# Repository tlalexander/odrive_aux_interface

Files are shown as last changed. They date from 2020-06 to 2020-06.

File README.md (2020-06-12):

Meow I'm a cat.

This repo contains Kicad files for an Odrive auxiliary interface board.

This board plugs in to your Odrive and gives you JST-XH connectors for the GPIO.

This is version 1.2 (see previous commits for older versions).
1.2 uses an ethernet cable and RS-485 for interface for communications.
1.2 also features an e-stop circuit which must be driven by a square wave.

See parts_list.txt for a parts list for the older V1.1. See the current schematic for part info on 1.2.

Order the older V1.1 PCB directly from OSHPark here:
https://oshpark.com/shared_projects/oXQvdpD9

This board was designed by Taylor Alexander for Twisted Fields LLC.
Big thanks to Daniel Theobald for funding the work.

This work is licensed CC0 aka Public Domain. Use this information for any purpose.

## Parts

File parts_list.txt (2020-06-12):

MY APOLOGIES BUT THIS DOCUMENT IS OUT OF DATE FOR v1.2

36-5015CT-ND‎
‎5015‎
Keystone Electronics
PC TEST POINT MINIATURE 

455-2270-ND‎
‎B5B-XH-A(LF)(SN)‎
JST Sales America Inc.
CONN HEADER VERT 5POS 2.5MM

952-3302-ND‎
‎M20-9991245‎
Harwin Inc.
CONN HEADER VERT 12POS 2.54MM 

-------

455-3241-ND‎
‎ASXHSXH22K305‎
JST Sales America Inc.
JUMPER SXH-001T-P0.6 X2 12"

455-2268-ND‎
‎XHP-5‎
JST Sales America Inc.
CONN HOUSING 2.5MM 5POS

455-2266-ND
JST XH 2 Pin Housing

455-2219-ND
JST XH 3 Pin Housing

455-2267-ND
JST XH 4 Pin Housing

-------------

1080-1602-1-ND
EL814S1(A)(TA)-V
OPTOISOLTR 5KV TRANSISTOR 4-SMD 

P20KDACT-ND
20k 0805 resistor

455-2271-ND‎
‎B6B-XH-A(LF)(SN)‎
JST Sales America Inc.
CONN HEADER VERT 6POS 2.5MM

455-2249-ND‎
‎B4B-XH-A(LF)(SN)‎
JST Sales America Inc.
CONN HEADER VERT 4POS 2.5MM

455-2248-ND‎
‎B3B-XH-A(LF)(SN)‎
JST Sales America Inc.
CONN HEADER VERT 3POS 2.5MM

455-2247-ND‎
‎B2B-XH-A(LF)(SN)‎
JST Sales America Inc.
CONN HEADER VERT 2POS 2.5MM

609-5100-ND‎
‎68000-220HLF‎
Amphenol ICC (FCI)
CONN HEADER VERT 20POS 2.54MM

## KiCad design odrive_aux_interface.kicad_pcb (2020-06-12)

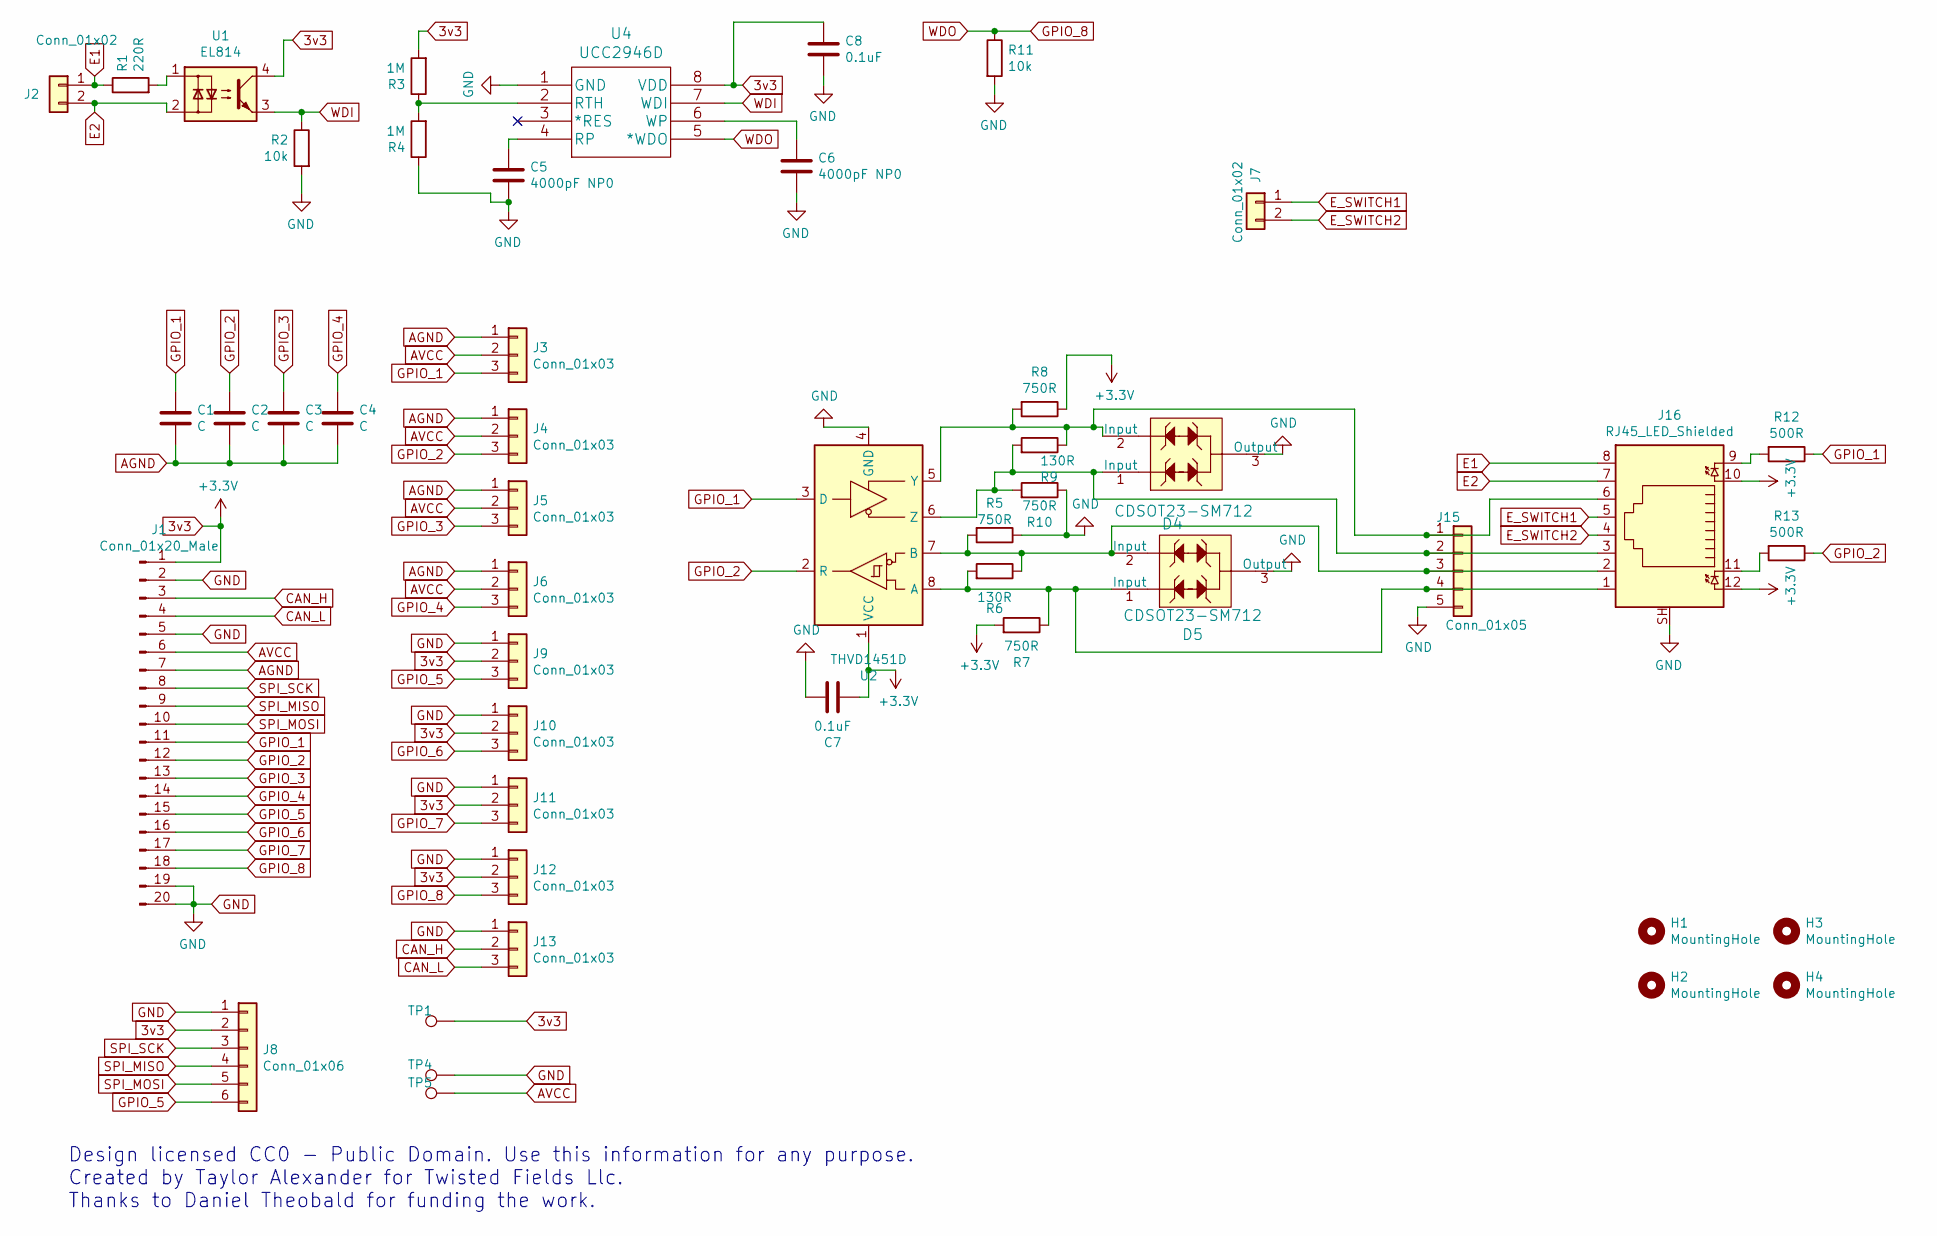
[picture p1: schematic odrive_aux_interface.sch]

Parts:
C1, C2, C3, C4: C; C_0805_2012Metric
C5, C6: 4000pF NP0; C_0805_2012Metric
C7, C8: 0.1uF; C_0805_2012Metric
D4, D5: CDSOT23-SM712; SOT-23-3; MPN CDSOT23-SM712; Digikey CDSOT23-SM712CT-ND
H1, H2, H3, H4: MountingHole; MountingHole_3.2mm_M3
J1: Conn_01x20_Male; PinHeader_1x20_P2.54mm_Vertical
J2, J7: Conn_01x02; JST_XH_B2B-XH-A_1x02_P2.50mm_Vertical
J3, J4, J5, J6, J9, J10, J11, J12, J13: Conn_01x03; JST_XH_B3B-XH-A_1x03_P2.50mm_Vertical
J8: Conn_01x06; JST_XH_B6B-XH-A_1x06_P2.50mm_Vertical
J15: Conn_01x05; JST_XH_B5B-XH-A_1x05_P2.50mm_Vertical; Digikey 455-1707-ND
J16: RJ45_LED_Shielded; RJ45_Amphenol_RJHSE538X
R1: 220R; R_0805_2012Metric
R2, R11: 10k; R_0805_2012Metric
R3, R4: 1M; R_0805_2012Metric
R5, R7, R8, R10: 750R; R_0805_2012Metric; Digikey RMCF0805FT750RCT-ND
R6, R9: 130R; R_0805_2012Metric; Digikey RMCF0805FT130RCT-ND
R12, R13: 500R; R_0805_2012Metric; Digikey RMCF0805FT750RCT-ND
TP1, TP4, TP5: TestPoint; TestPoint_Keystone_5015_Micro-Minature
U1: EL814; SO-4_7.6x3.6mm_P2.54mm
U2: THVD1451D; SOIC-8_3.9x4.9mm_P1.27mm; Digikey 296-THVD1451D-ND
U4: UCC2946D; SO-8_3.9x4.9mm_P1.27mm

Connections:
3v3: C7.1, C8.1, J1.1, J8.2, J9.2, J10.2, J11.2, J12.2, J16.10, J16.12, R3.2, R7.2, R8.1, TP1.1, U1.4, U2.1 (VCC), U4.8 (VDD)
AGND: C1.2, C2.2, C3.2, C4.2, J1.7, J3.1, J4.1, J5.1, J6.1
AVCC: J1.6, J3.2, J4.2, J5.2, J6.2, TP5.1
CAN_H: J1.3, J13.2
CAN_L: J1.4, J13.3
E1: J2.1, J16.8, R1.1
E2: J2.2, J16.7, U1.2
E_SWITCH1: J7.1, J16.5
E_SWITCH2: J7.2, J16.4
GND: C5.2, C6.2, C7.2, C8.2, D4.3 (Output), D5.3 (Output), J1.2, J1.5, J1.19, J1.20, J8.1, J9.1, J10.1, J11.1, J12.1, J13.1, J15.5, J16.SH, R2.2, R4.1, R5.1, R10.1, R11.2, TP4.1, U2.4 (GND), U4.1 (GND)
GPIO_1: C1.1, J1.11, J3.3, R12.1, U2.3 (D)
GPIO_2: C2.1, J1.12, J4.3, R13.1, U2.2 (R)
GPIO_3: C3.1, J1.13, J5.3
GPIO_4: C4.1, J1.14, J6.3
GPIO_5: J1.15, J8.6, J9.3
GPIO_6: J1.16, J10.3
GPIO_7: J1.17, J11.3
GPIO_8: J1.18, J12.3, R11.1, U4.5 (*WDO)
unnamed: C5.1, U4.4 (RP)
unnamed: C6.1, U4.6 (WP)
unnamed: D4.1 (Input), J15.2, J16.3, R9.2, R10.2, U2.6 (Z)
unnamed: D4.2 (Input), J15.1, J16.6, R8.2, R9.1, U2.5 (Y)
unnamed: D5.1 (Input), J15.4, J16.1, R6.2, R7.1, U2.8 (A)
unnamed: D5.2 (Input), J15.3, J16.2, R5.2, R6.1, U2.7 (B)
unnamed: J16.9, R12.2
unnamed: J16.11, R13.2
unnamed: R1.2, U1.1
unnamed: R3.1, R4.2, U4.2 (RTH)
SPI_MISO: J1.9, J8.4
SPI_MOSI: J1.10, J8.5
SPI_SCK: J1.8, J8.3
WDI: R2.1, U1.3, U4.7 (WDI)

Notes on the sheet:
Design licensed CC0 - Public Domain. Use this information for any purpose. Created by Taylor Alexander for Twisted Fields Llc. Thanks to Daniel Theobald for funding the work.

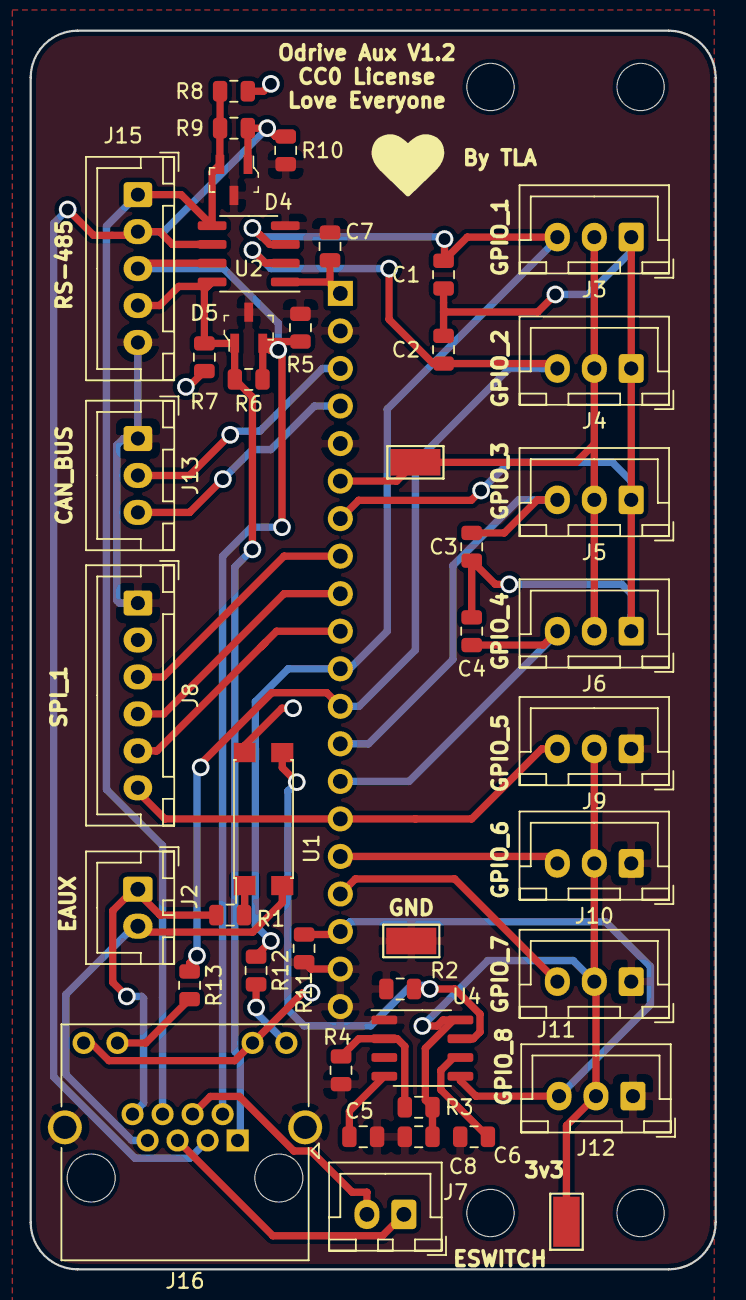
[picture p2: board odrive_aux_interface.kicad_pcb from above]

Board: 2 copper layers, 46.4 x 83.8 mm, 48 parts (1 on the bottom side), 32 nets.

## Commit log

2019-10-24 Initial Commit.
    [odrive_aux_interface.kicad_pcb, odrive_aux_interface.sch]
2020-06-12 Update to v1.2, add gerbers.
    [odrive_aux_interface-B_Cu.gbr, odrive_aux_interface-B_Mask.gbr, odrive_aux_interface-B_SilkS.gbr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]

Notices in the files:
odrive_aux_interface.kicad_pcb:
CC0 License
